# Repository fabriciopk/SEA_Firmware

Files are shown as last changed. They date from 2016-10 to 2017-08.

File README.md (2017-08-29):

# SEA_Firmware
Firmware for series elastic actuator, this board contains a stm32f103 microcontroller

#Installation(Upload using arduino IDE)

- Download arduino [IDE](https://www.arduino.cc/en/Main/Software)
- Download zip file containing the STM32 files from [here](https://github.com/fabriciopk/Arduino_STM32/archive/master.zip)
- Unzip in arduino hardware folder (arduino-1.6.xx/hardware/) and rename to Arduino_STM32
- Run the arduino IDE, and on the Tools menu, select the Boards manager (Tools > Boards > Boards Manager), and install the Arduino Zero(Arduino SAMD boards 32 bits cortex M3) from the list of available boards. You must do this step, it installs the arm-none-eabi-g++ toolchain!
- Copy AS5048A and DynamixelProtocol from [lib](https://github.com/fabriciopk/SEA_Firmware/tree/master/lib) folder to (arduino-1.6.xx/libraries/)
- Change the line #define BOARD_HAVE_SERIALUSB 0 in the file arduino-1.6.xx/hardware/STM32F1/cores/maple/boards.h 

#Setup Arduino IDE and board upload pins
- Board:STM32F103C Generic
- Variant:STM32F103C8
- Upload method: Stlink
- Open [src/src.ino](https://github.com/fabriciopk/SEA_Firmware/blob/master/src/src.ino)
- Pins for SWD(stlink v.2) setup:

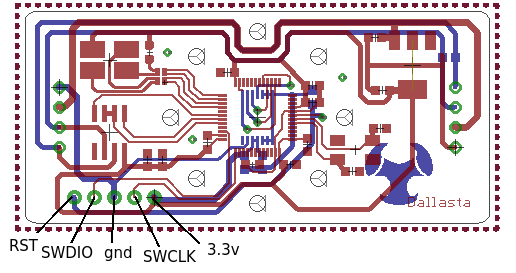
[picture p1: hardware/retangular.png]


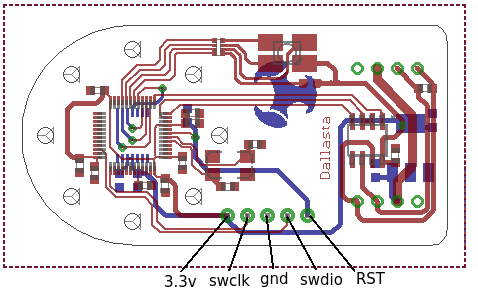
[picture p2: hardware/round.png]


NOTE: top-side of board.
#Board settings
```c++
#define SEA_ID 105 //define the board id in rs485 network
#define INVERTED
...
#define SEA_RECT //Type of the board, coment if is the rounded board
...
```
#Testing(linux)

Plug usb2Dinamyxel, power on the board.
```bash
cd test_board
make
./dynamixel_test ID_board
```

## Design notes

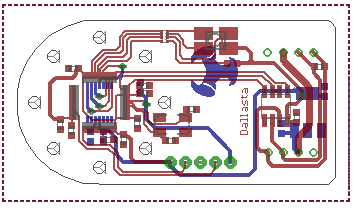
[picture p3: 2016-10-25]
hardware/eagle_files/OUT/sad.png

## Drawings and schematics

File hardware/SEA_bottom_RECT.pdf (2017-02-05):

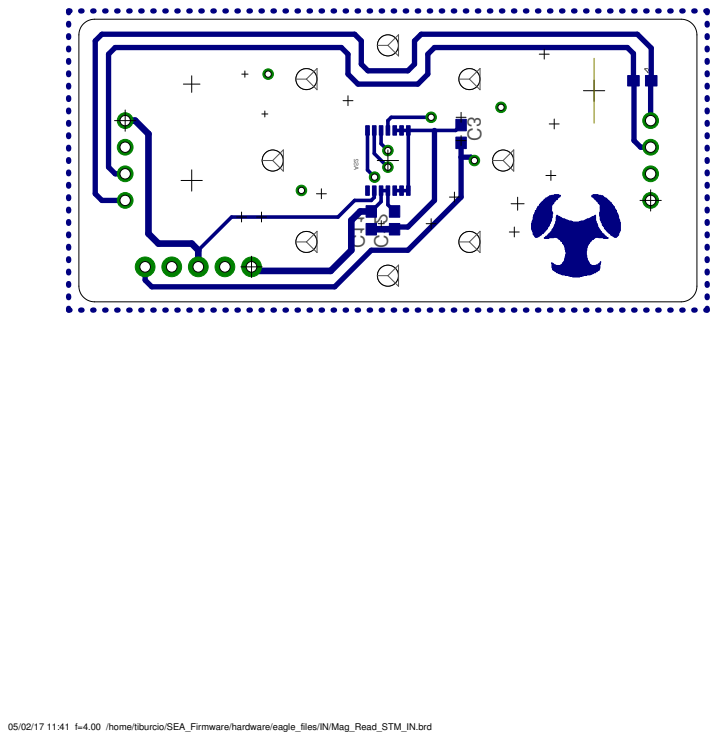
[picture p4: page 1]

05/02/17 11:41 f=4.00 /home/tiburcio/SEA_Firmware/hardware/eagle_files/IN/Mag_Read_STM_IN.brd

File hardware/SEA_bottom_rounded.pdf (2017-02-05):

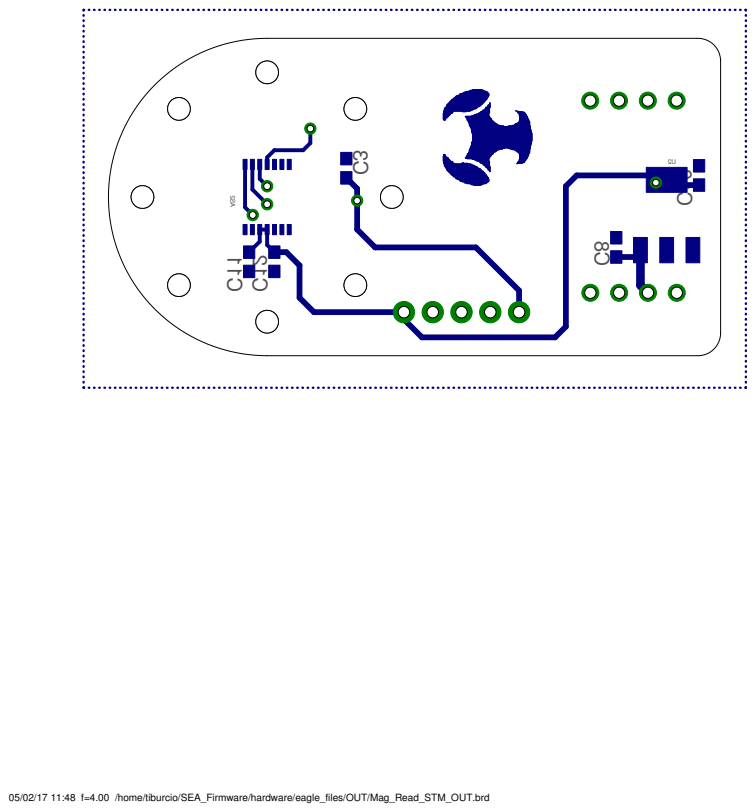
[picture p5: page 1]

05/02/17 11:48 f=4.00 /home/tiburcio/SEA_Firmware/hardware/eagle_files/OUT/Mag_Read_STM_OUT.brd

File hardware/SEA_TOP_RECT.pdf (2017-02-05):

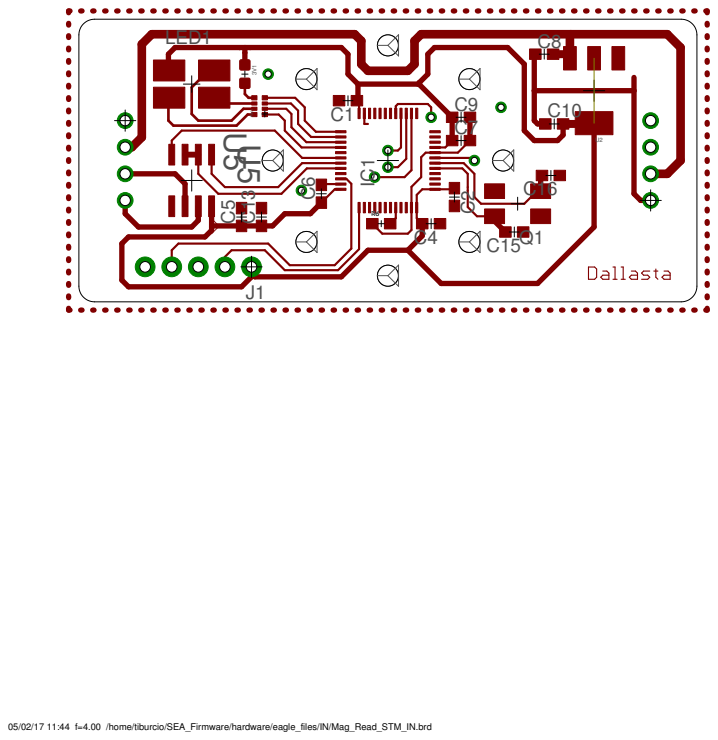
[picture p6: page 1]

05/02/17 11:44 f=4.00 /home/tiburcio/SEA_Firmware/hardware/eagle_files/IN/Mag_Read_STM_IN.brd

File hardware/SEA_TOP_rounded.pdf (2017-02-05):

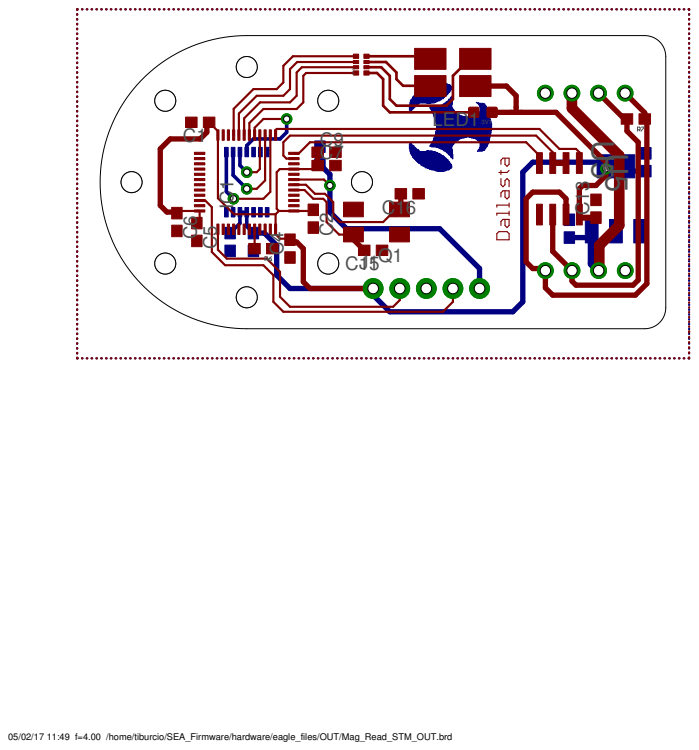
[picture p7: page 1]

05/02/17 11:49 f=4.00 /home/tiburcio/SEA_Firmware/hardware/eagle_files/OUT/Mag_Read_STM_OUT.brd

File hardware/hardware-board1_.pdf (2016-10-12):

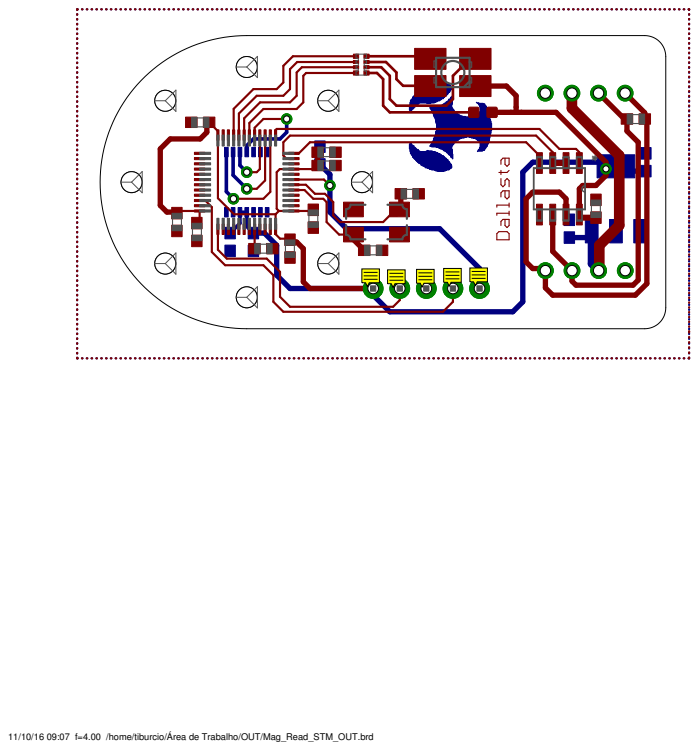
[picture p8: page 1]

11/10/16 09:07 f=4.00 /home/tiburcio/Área de Trabalho/OUT/Mag_Read_STM_OUT.brd

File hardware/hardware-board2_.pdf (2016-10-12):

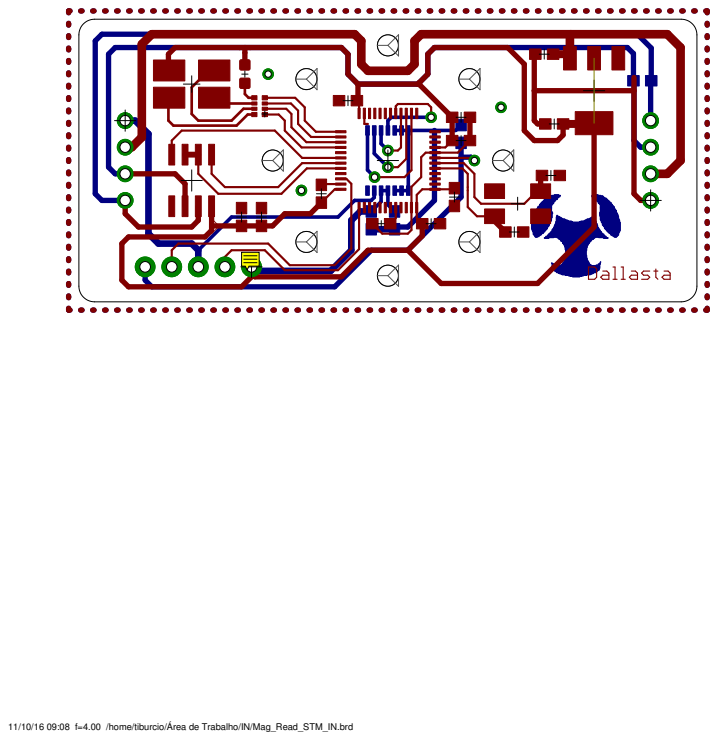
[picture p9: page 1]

11/10/16 09:08 f=4.00 /home/tiburcio/Área de Trabalho/IN/Mag_Read_STM_IN.brd

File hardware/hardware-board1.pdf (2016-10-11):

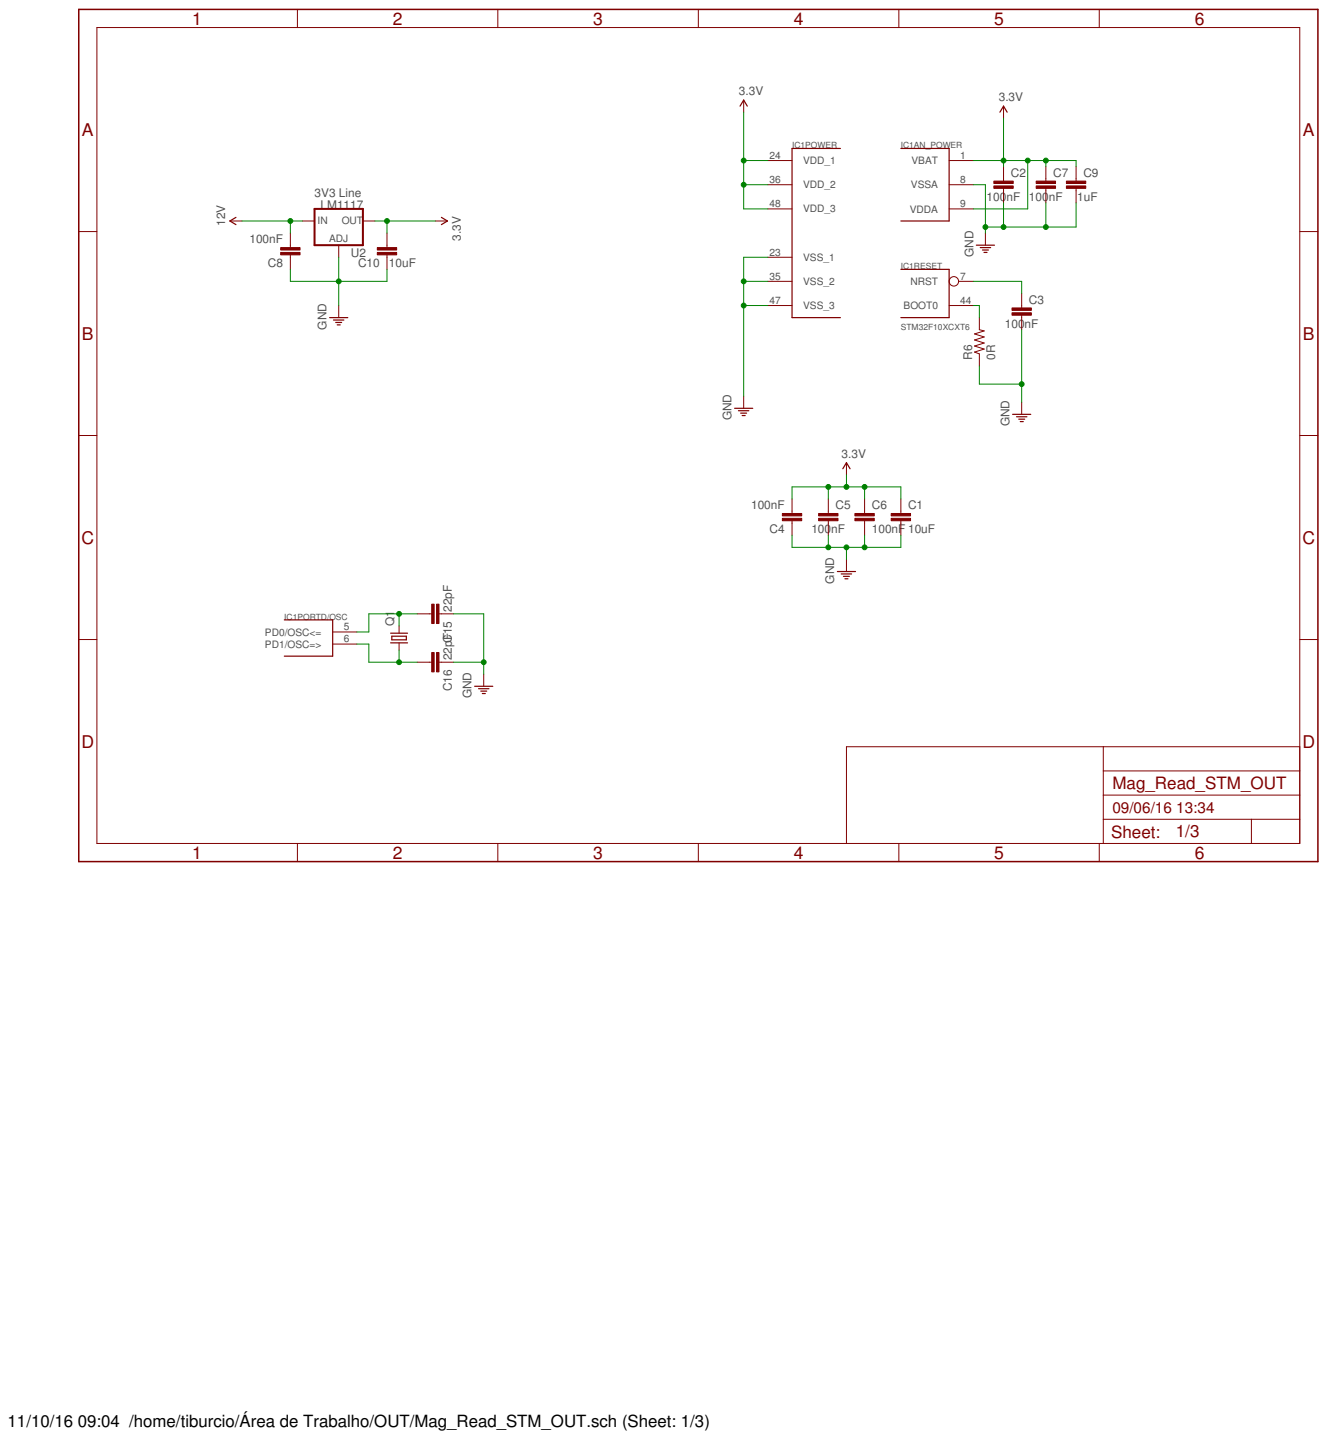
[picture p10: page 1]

11/10/16 09:04 /home/tiburcio/Área de Trabalho/OUT/Mag_Read_STM_OUT.sch (Sheet: 1/3)

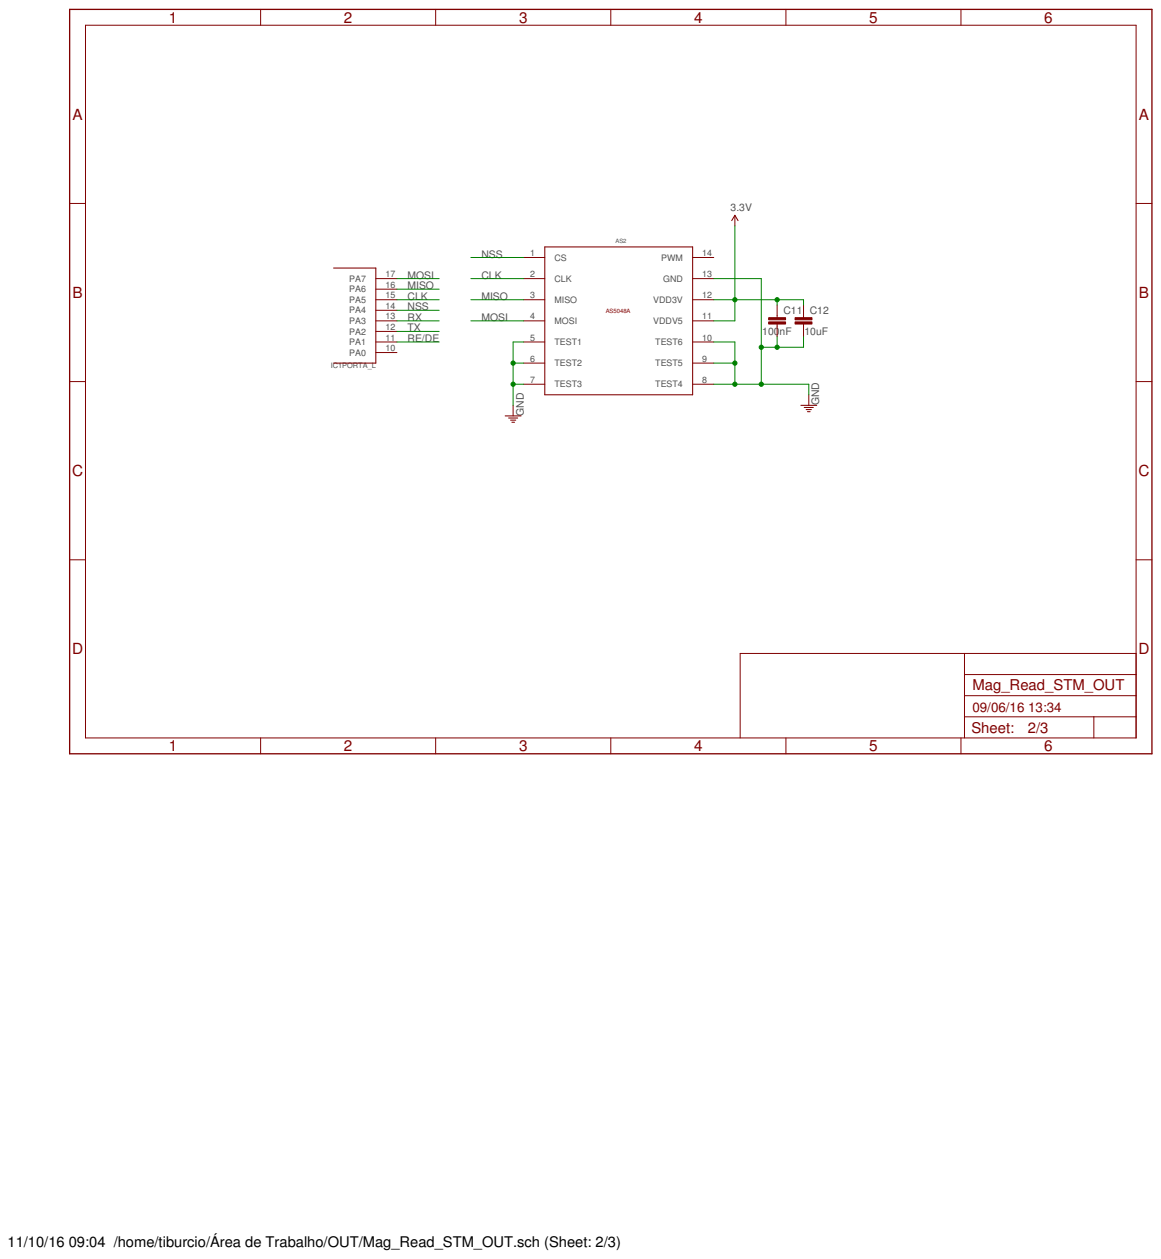
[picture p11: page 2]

11/10/16 09:04 /home/tiburcio/Área de Trabalho/OUT/Mag_Read_STM_OUT.sch (Sheet: 2/3)

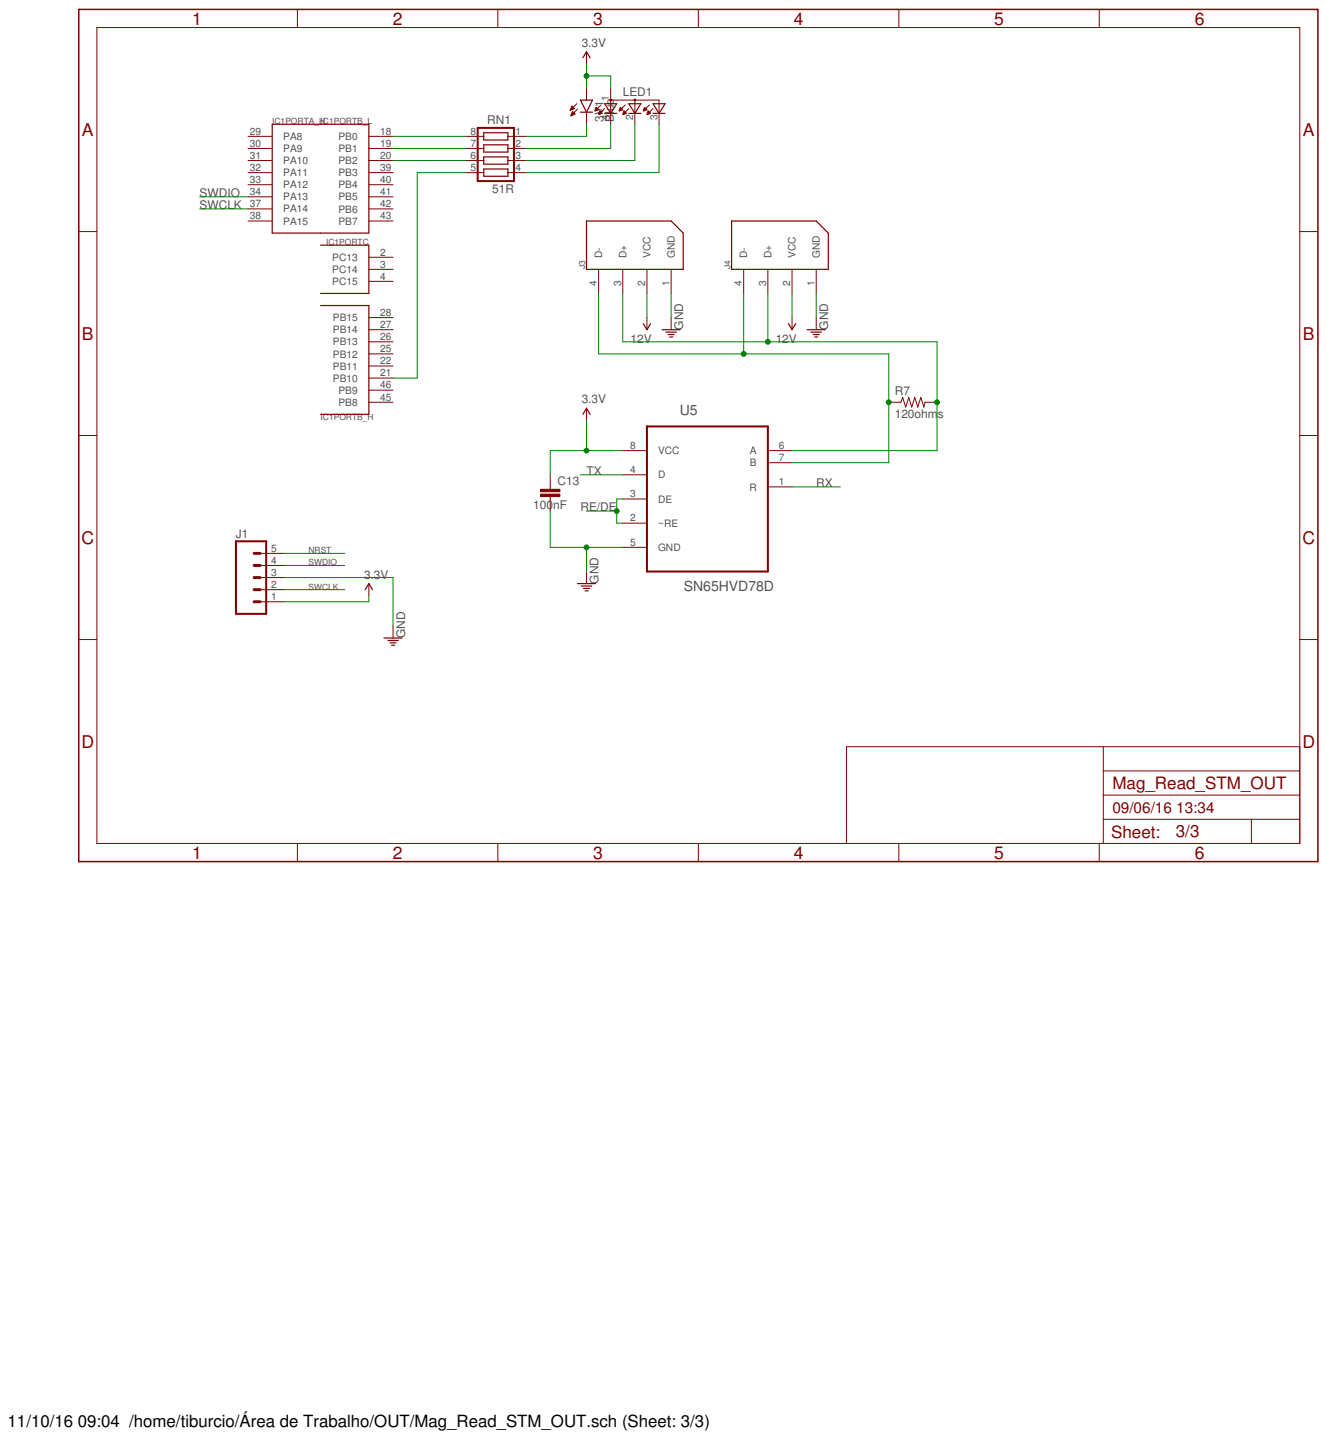
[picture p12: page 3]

19 PB2 7 | 2
20 PB3 6 | 3
39 PB4 5 | 4

11/10/16 09:04 /home/tiburcio/Área de Trabalho/OUT/Mag_Read_STM_OUT.sch (Sheet: 3/3)

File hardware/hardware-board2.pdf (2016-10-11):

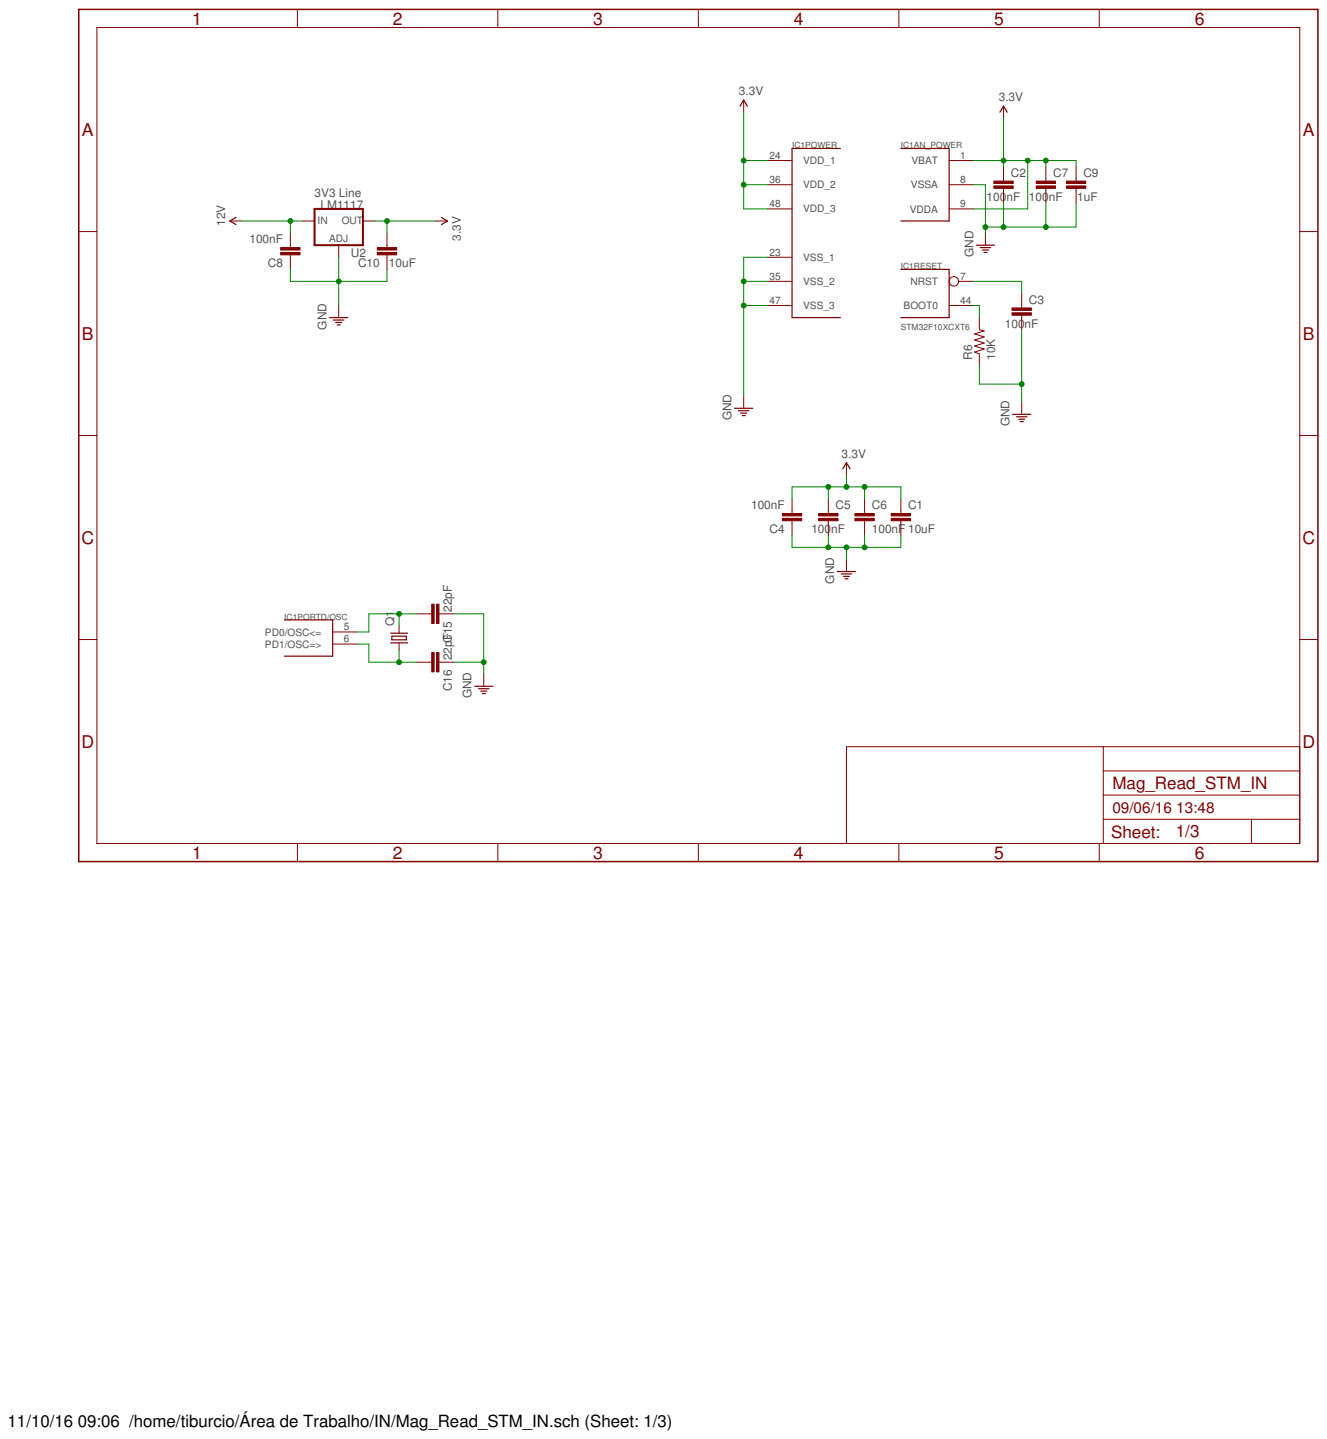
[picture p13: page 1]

11/10/16 09:06 /home/tiburcio/Área de Trabalho/IN/Mag_Read_STM_IN.sch (Sheet: 1/3)

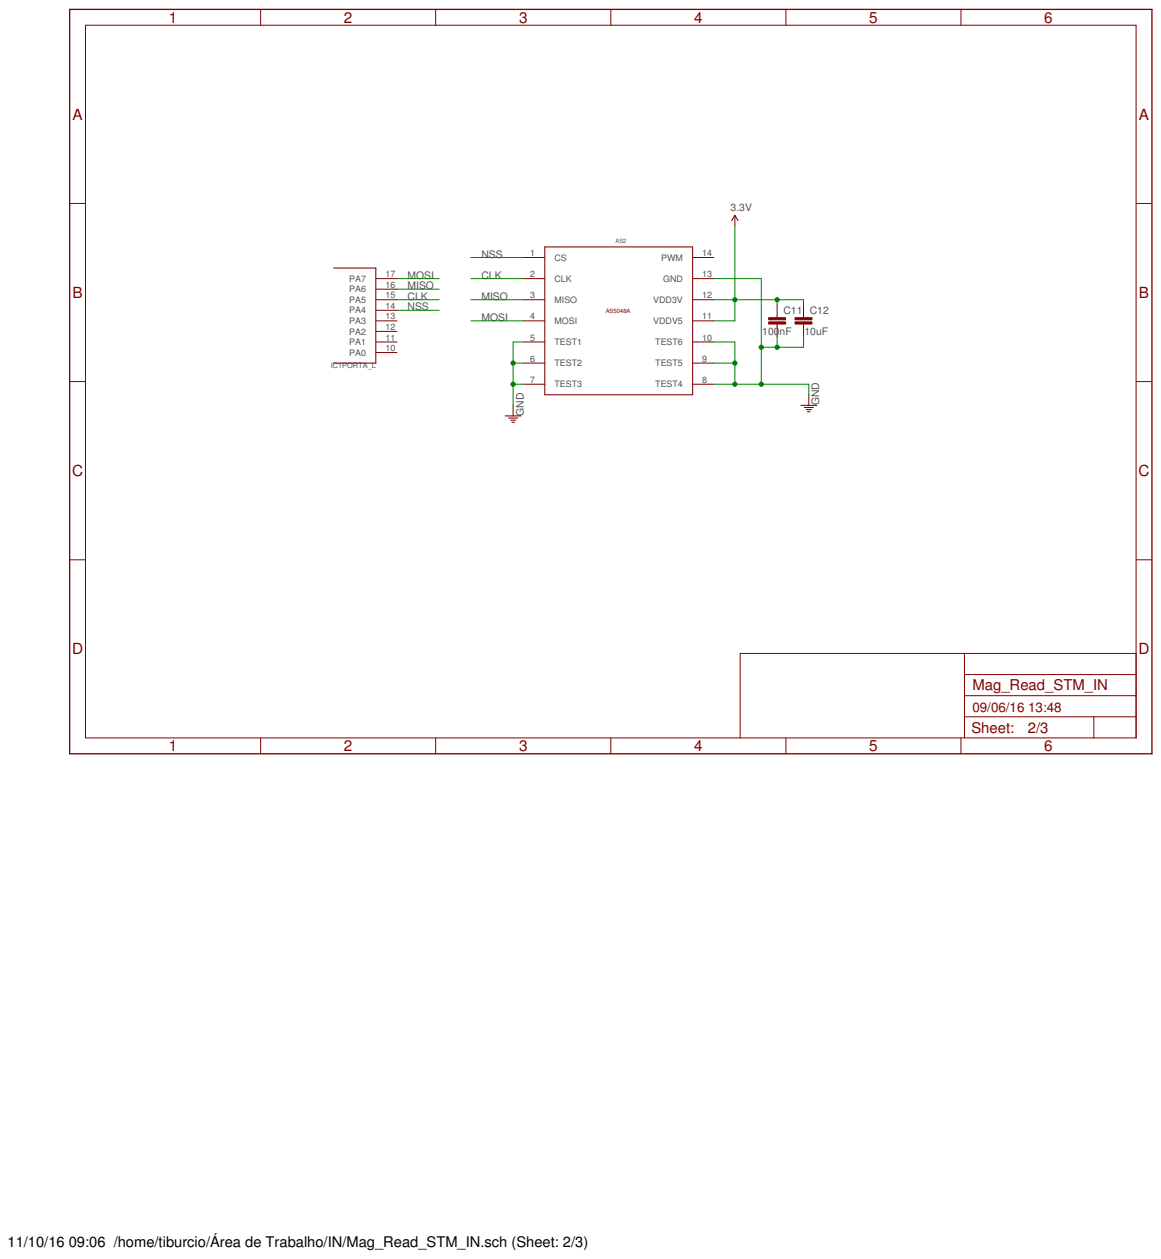
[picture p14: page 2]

11/10/16 09:06 /home/tiburcio/Área de Trabalho/IN/Mag_Read_STM_IN.sch (Sheet: 2/3)

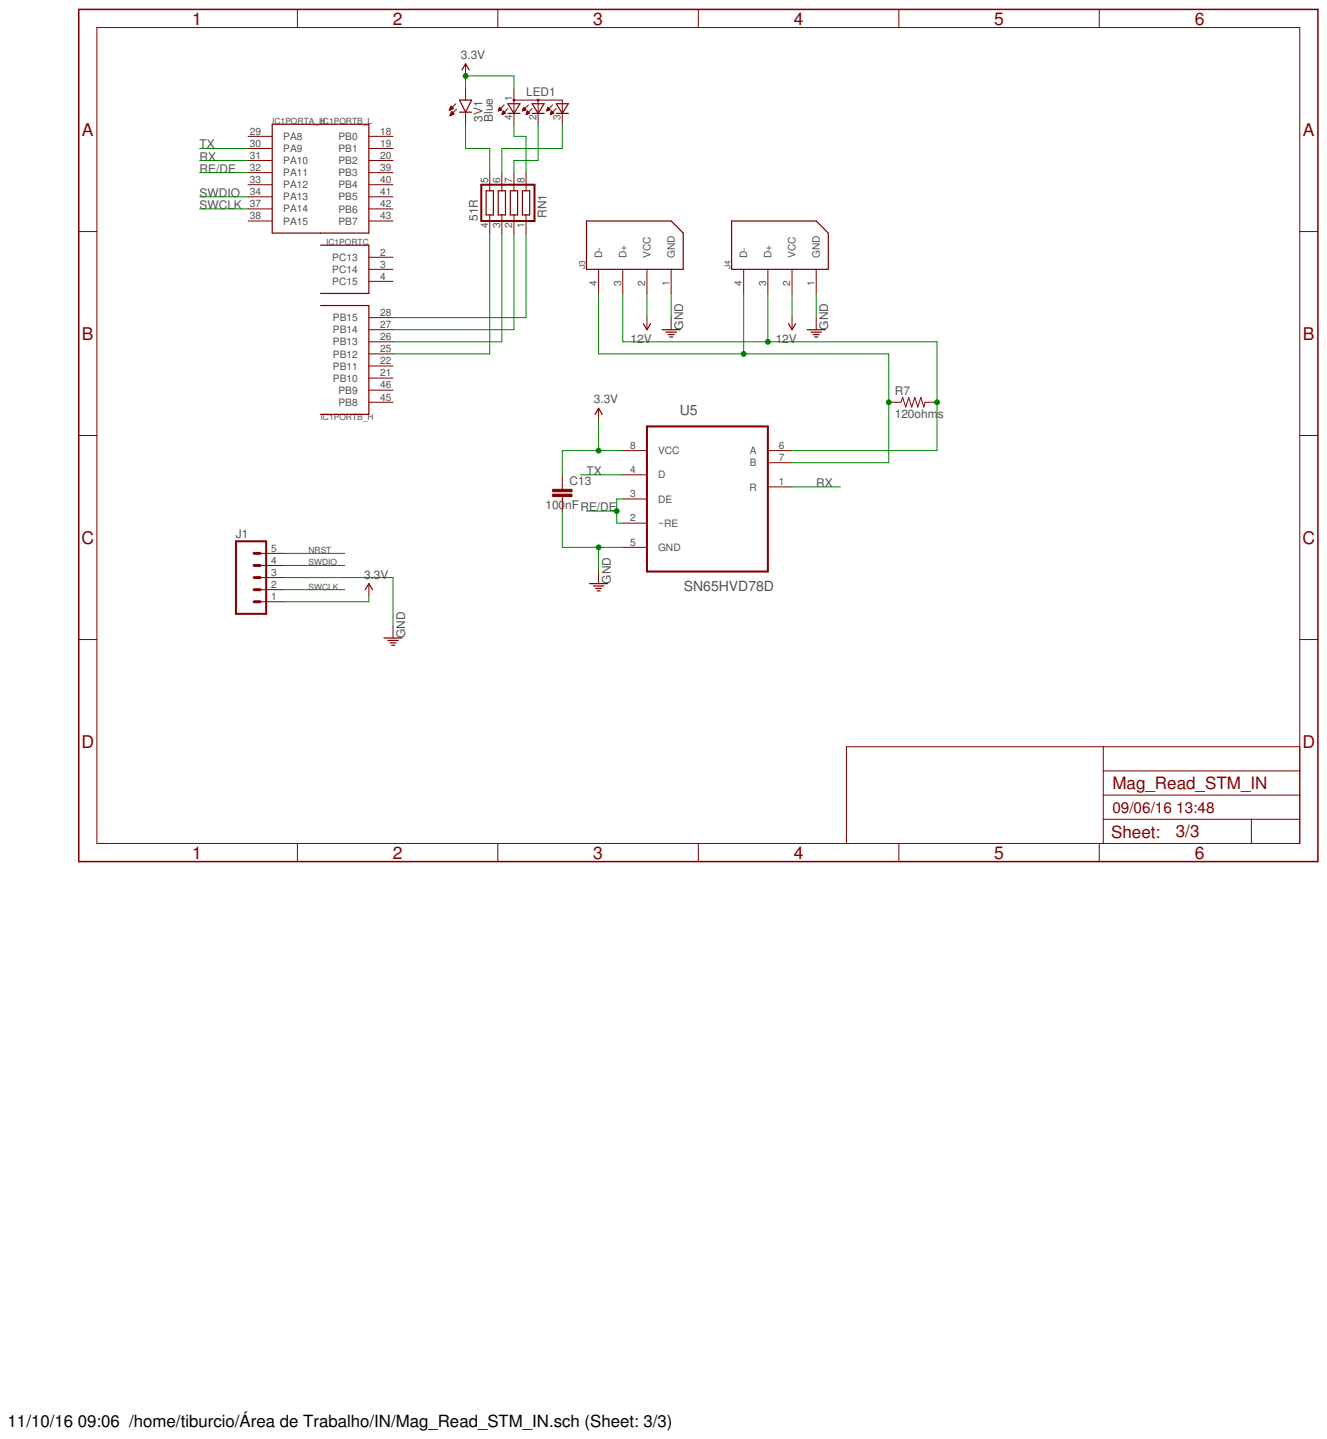
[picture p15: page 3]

27 PB15
26 PB14

11/10/16 09:06 /home/tiburcio/Área de Trabalho/IN/Mag_Read_STM_IN.sch (Sheet: 3/3)

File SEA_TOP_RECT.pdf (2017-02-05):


05/02/17 11:43 f=4.00 /home/tiburcio/SEA_Firmware/hardware/eagle_files/IN/Mag_Read_STM_IN.brd

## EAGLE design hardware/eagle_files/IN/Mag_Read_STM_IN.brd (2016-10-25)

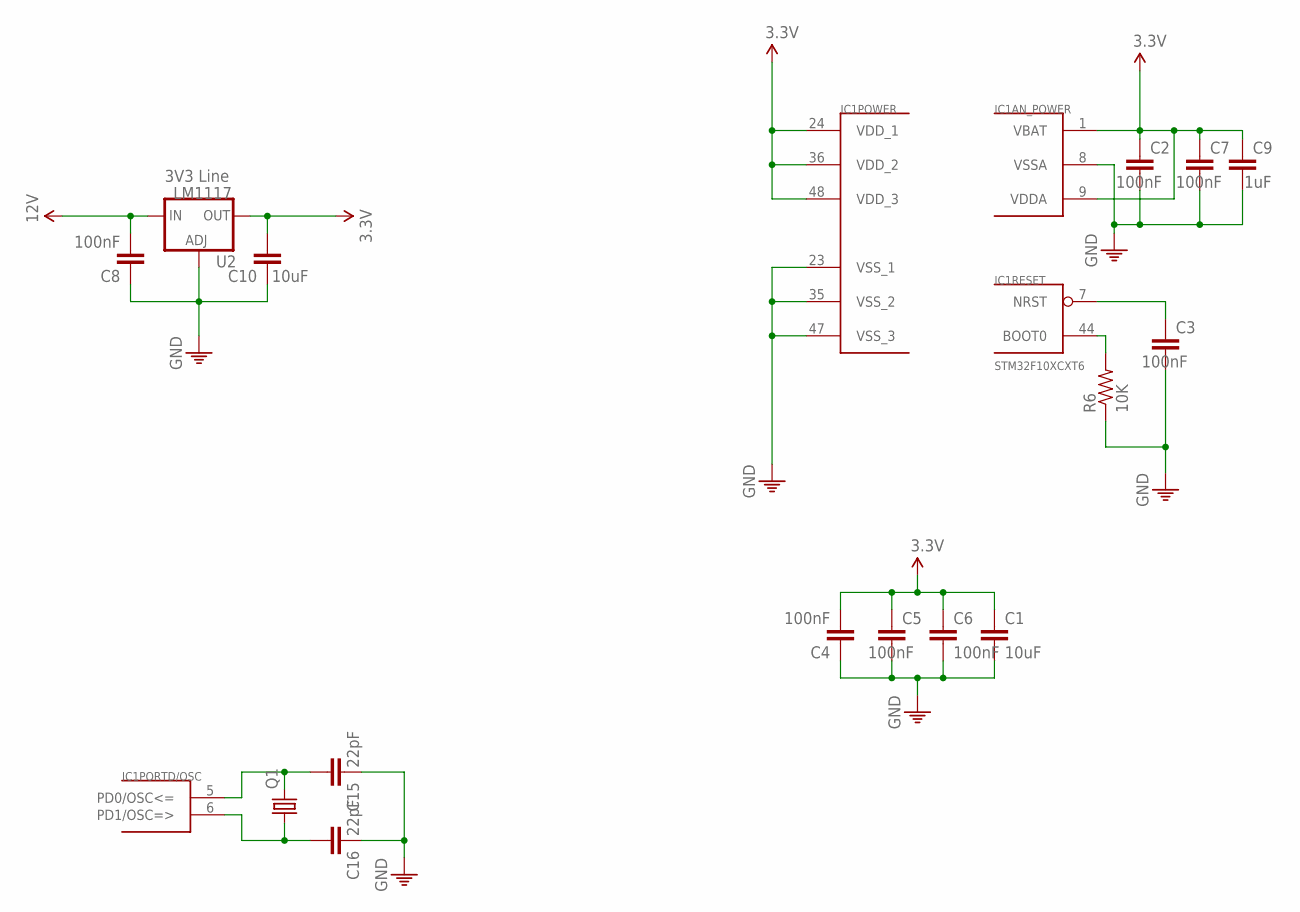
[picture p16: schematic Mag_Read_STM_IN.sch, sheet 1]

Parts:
C1, C10: 10uF; C0603
C2, C3, C4, C5, C6, C7, C8: 100nF; C0603
C9: 1uF; C0603
C15, C16: 22pF; C0603
IC1: STM32F10XCXT6; TQFP48
Q1: CRYSTALCTS406; CTS406
R6: 10K; 0603-RES
U2: LM1117; SOT223

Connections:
3.3V: C1.1, C2.1, C4.2, C5.1, C6.1, C7.1, C9.1, C10.2, IC1.1 (VBAT), IC1.9 (VDDA), IC1.24 (VDD_1), IC1.36 (VDD_2), IC1.48 (VDD_3), U2.2 (OUT), U2.4 (OUT); also elsewhere on the board
12V: C8.2, U2.3 (IN); also elsewhere on the board
GND: C1.2, C2.2, C3.2, C4.1, C5.2, C6.2, C7.2, C8.1, C9.2, C10.1, C15.1, C16.1, IC1.8 (VSSA), IC1.23 (VSS_1), IC1.35 (VSS_2), IC1.47 (VSS_3), R6.1, U2.1 (ADJ); also elsewhere on the board
unnamed: C15.2, IC1.5 (PD0/OSC<=), Q1.3 (2)
unnamed: C16.2, IC1.6 (PD1/OSC=>), Q1.1
unnamed: IC1.44 (BOOT0), R6.2
NRST: C3.1, IC1.7 (NRST); also elsewhere on the board

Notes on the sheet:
3V3 Line

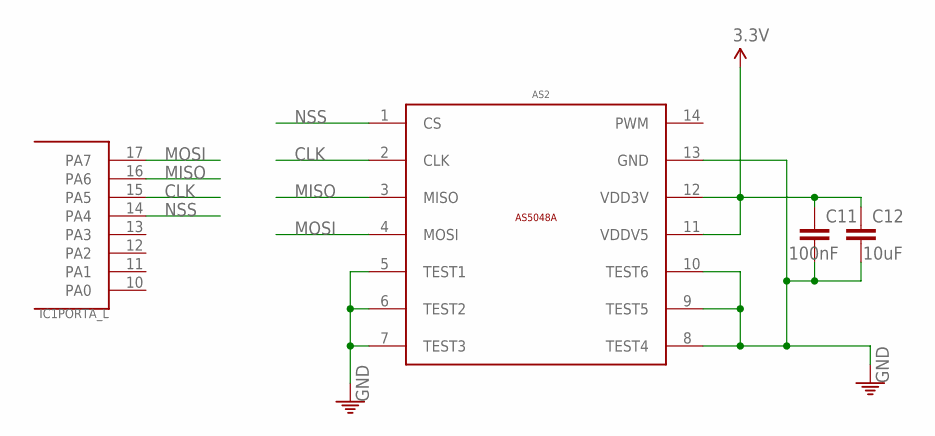
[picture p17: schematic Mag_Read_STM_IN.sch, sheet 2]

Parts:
AS2: AS5048A_MAGNETIC_ROTARY_ENCODERTSSOP14; AS5048A_14-TSSOP
C11: 100nF; C0603
C12: 10uF; C0603
IC1: STM32F10XCXT6; TQFP48

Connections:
3.3V: AS2.11 (VDDV5), AS2.12 (VDD3V), C11.1, C12.1; also elsewhere on the board
CLK: AS2.2 (CLK), IC1.15 (PA5)
GND: AS2.5 (TEST1), AS2.6 (TEST2), AS2.7 (TEST3), AS2.8 (TEST4), AS2.9 (TEST5), AS2.10 (TEST6), AS2.13 (GND), C11.2, C12.2; also elsewhere on the board
MISO: AS2.3 (MISO), IC1.16 (PA6)
MOSI: AS2.4 (MOSI), IC1.17 (PA7)
NSS: AS2.1 (CS), IC1.14 (PA4)

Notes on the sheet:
MISO
MOSI
NSS
CLK

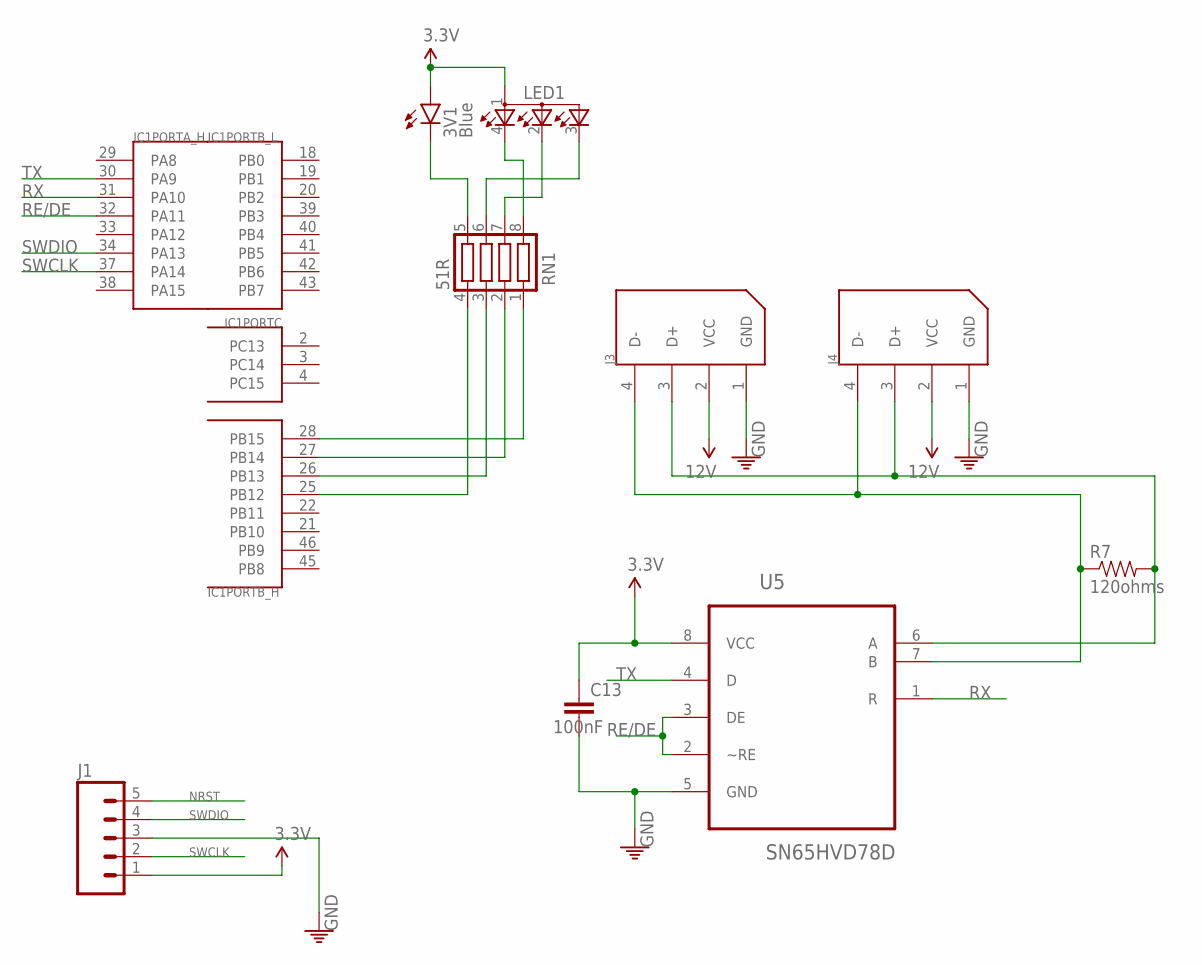
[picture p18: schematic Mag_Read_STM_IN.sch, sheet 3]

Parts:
3V1: Blue; LED-0603
C13: 100nF; C0603
IC1: STM32F10XCXT6; TQFP48
J1: M05PTH; 1X05
J3, J4: 22-03-5045; 5267-4
LED1: TOPLED-3; P-LCC-4-3
R7: 120ohms; 0603-RES
RN1: 51R; CAY10-XXXJ4
U5: SN65HVD78D; SOIC127P600X175-8N

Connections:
3.3V: 3V1.A, C13.1, J1.1, LED1.1 (A2), U5.8 (VCC); also elsewhere on the board
12V: J3.2 (VCC), J4.2 (VCC); also elsewhere on the board
D+: J3.3 (D+), J4.3 (D+), R7.2, U5.6 (A)
D-: J3.4 (D-), J4.4 (D-), R7.1, U5.7 (B)
GND: C13.2, J1.3, J3.1 (GND), J4.1 (GND), U5.5 (GND); also elsewhere on the board
unnamed: 3V1.C, RN1.5
unnamed: IC1.28 (PB15), RN1.1
unnamed: IC1.27 (PB14), RN1.2
unnamed: IC1.26 (PB13), RN1.3
unnamed: LED1.3 (CGREEN), RN1.6
unnamed: LED1.2 (CBLUE), RN1.7
unnamed: LED1.4 (CRED), RN1.8
unnamed: IC1.25 (PB12), RN1.4
NRST: J1.5; also elsewhere on the board
RE/DE: IC1.32 (PA11), U5.2 (~RE), U5.3 (DE)
RX: IC1.31 (PA10), U5.1 (R)
SWCLK: IC1.37 (PA14), J1.2
SWDIO: IC1.34 (PA13), J1.4
TX: IC1.30 (PA9), U5.4 (D)

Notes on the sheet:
RE/DE
SWCLK
SWDIO
NRST

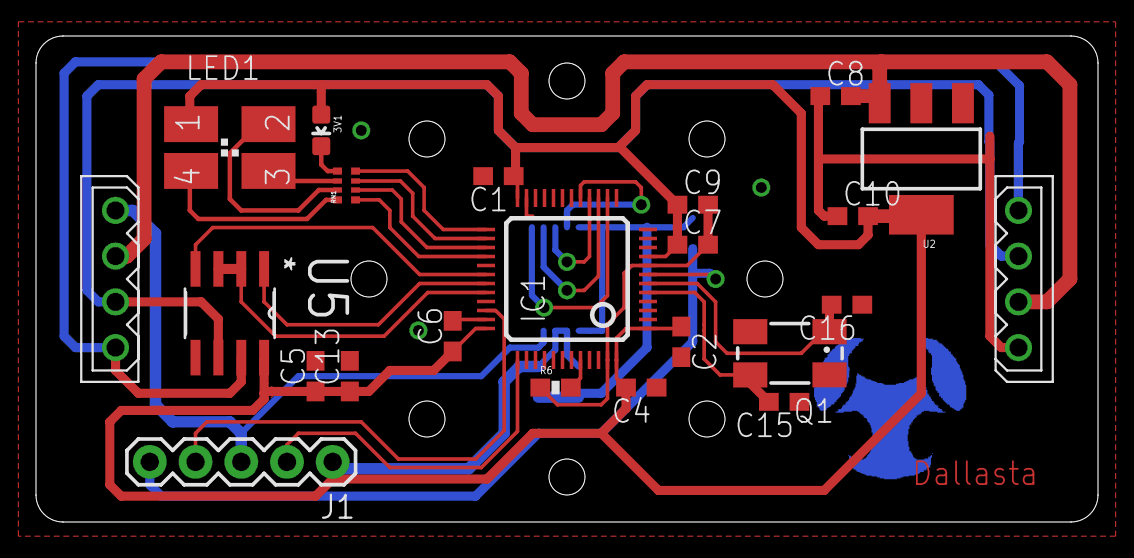
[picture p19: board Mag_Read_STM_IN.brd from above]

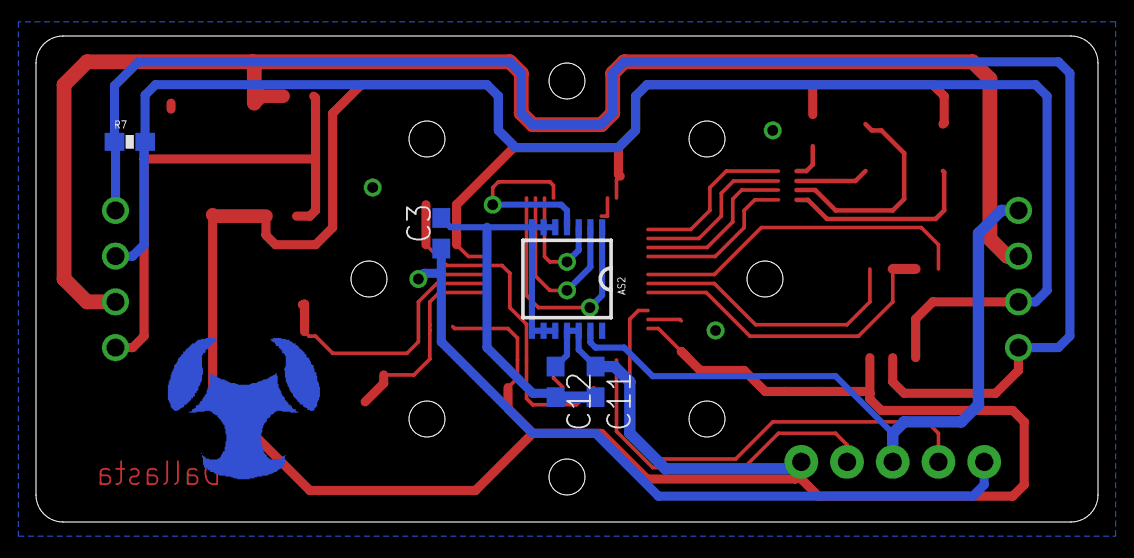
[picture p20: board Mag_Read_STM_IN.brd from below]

Board: 2 copper layers, 59.0 x 27.0 mm, 28 parts (5 on the bottom side), 26 nets.

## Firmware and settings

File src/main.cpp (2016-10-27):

#include <DynamixelProtocol.h>
#include <AS5048A.h>

//TODO check if serial of maple core is in the correct pins
//HardwareSerial Serial1(&rx_buffer1, &UBRR1H, &UBRR1L, &UCSR1A, &UCSR1B, &UDR1, RXEN1, TXEN1, RXCIE1, UDRE1, U2X1);

#define SEA_ID 105
#define INVERTED
#define SEA_INSTRUCTION 0x24

#define SEA_RECT

#ifdef SEA_RECT

#define LED PB12
#define LED_RED PB14
#define LED_BLUE PB15
#define LED_GREEN PB13
#define SERIAL Serial1 //Tem que mudar dentro da biblioteca do dynamixel tambem (Serial)
#define EN PA11

#else

#define LED PB0
#define LED_RED PB2
#define LED_BLUE PB1
#define LED_GREEN PB10
#define SERIAL Serial2 //Tem que mudar dentro da biblioteca do dynamixel tambem (Serial)
#define EN PA1

#endif

#define SPI_NSS PA4
#define BAUDRATE_DX 1000000

int RGB[3] = {LED_RED, LED_GREEN, LED_BLUE};
int color = 0;

AS5048A mag(SPI_NSS);
DynamixelProtocol dxl(BAUDRATE_DX, SEA_ID, SERIAL);

void blink(int times)
{
  for (int i = 0 ; i < times ; i++)
  {
    digitalWrite(LED, LOW);
    delay(125);
    digitalWrite(LED, HIGH);
    delay(125);
  }
  delay(500);
}

void setup()
{
  delay(1000);
  pinMode(LED, OUTPUT);
  pinMode(LED_RED, OUTPUT);
  pinMode(LED_GREEN, OUTPUT);
  pinMode(LED_BLUE, OUTPUT);
  //Enable rs485
  pinMode(EN, OUTPUT);
  digitalWrite(EN, LOW);

  mag.init();
  dxl.init();
  blink(SEA_ID - 100);
  digitalWrite(LED_RED, HIGH);
  digitalWrite(LED_GREEN, HIGH);
  digitalWrite(LED_BLUE, HIGH);
}

void loop() {
#ifndef INVERTED
  word val = mag.getRawRotation();
#else
  word val = 8192 - mag.getRawRotation();
#endif
  dxl.checkMessages();
  if (dxl.instruction != DXL_NO_DATA)
  {

    switch (dxl.instruction)
    {
      case DXL_PING:
        digitalWrite(EN, HIGH);
        dxl.sendStatusPacket(0x00, NULL, 0);
        SERIAL.waitDataToBeSent();
        digitalWrite(EN, LOW);
        break;
      case DXL_READ_DATA:
        if (dxl.total_parameters == 2 && dxl.parameters[1] == 2)
        {
          unsigned char values[2];
          switch (dxl.parameters[0])
          {
            case SEA_INSTRUCTION:
              values[0] = (unsigned char)val;
              values[1] = (unsigned char)(val >> 8);
              digitalWrite(LED, HIGH);
              break;
            case 0x00:
              values[0] = 54;
              values[1] = 1;
              break;
            case 0x01:
              values[0] = 0;
              values[1] = 1;
              break;
            default:
              values[0] = 0;
              values[1] = 0;
              break;
          }
          digitalWrite(EN, HIGH);
          dxl.sendStatusPacket(0x00, values, 2);
          SERIAL.waitDataToBeSent();
          digitalWrite(EN, LOW);
          digitalWrite(RGB[color], LOW);
          color = (color + 1) % 3;
          digitalWrite(RGB[color], HIGH);
        }
        break;
      case DXL_WRITE_DATA:
        break;
      case DXL_REG_WRITE:
        break;
      case DXL_ACTION:
        break;
      case DXL_RESET:
        break;
      case DXL_SYNC_WRITE:
        break;
      default:
        break;
    }
  } else {
    digitalWrite(LED_RED, HIGH);
    digitalWrite(LED_GREEN, HIGH);
    digitalWrite(LED_BLUE, HIGH);
    digitalWrite(LED, HIGH);
  }
  digitalWrite(LED, HIGH);
}

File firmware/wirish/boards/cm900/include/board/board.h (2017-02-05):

/******************************************************************************
 * The MIT License
 *
 * Copyright (c) 2011 LeafLabs, LLC.
 *
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
 * THE SOFTWARE IS PROVIDED "AS IS", WITHOUT WARRANTY OF ANY KIND,
 * EXPRESS OR IMPLIED, INCLUDING BUT NOT LIMITED TO THE WARRANTIES OF
 * MERCHANTABILITY, FITNESS FOR A PARTICULAR PURPOSE AND
 * NONINFRINGEMENT. IN NO EVENT SHALL THE AUTHORS OR COPYRIGHT HOLDERS
 * BE LIABLE FOR ANY CLAIM, DAMAGES OR OTHER LIABILITY, WHETHER IN AN
 * ACTION OF CONTRACT, TORT OR OTHERWISE, ARISING FROM, OUT OF OR IN
 * CONNECTION WITH THE SOFTWARE OR THE USE OR OTHER DEALINGS IN THE
 * SOFTWARE.
 *****************************************************************************/


/*
 * CM900.h
 *
 *  Created on: 2012. 10. 14.
 *      Author: ROBOTIS[sm6787@robotis.com]
 *      ported from maple.h(leaflabs.com)
 *      @brief  Private include file for cm-900 in boards.h
 */

#ifndef CM_900_H_
#define CM_900_H_

//#include "gpio.h"


#define CYCLES_PER_MICROSECOND  72
#define SYSTICK_RELOAD_VAL      71999 /* takes a cycle to reload */
/*
 * [ROBOTIS][CHANGE] CM-900 Do not have built-in button.
 * 2013-04-22
 * */
#define BOARD_BUTTON_PIN        23//38
#define BOARD_LED_PIN           16

/* Number of USARTs/UARTs whose pins are broken out to headers */
//#define BOARD_NR_USARTS         3

/* Default USART pin numbers (not considering AFIO remap) */
#define BOARD_USART1_TX_PIN     9   //D9(PA9)
#define BOARD_USART1_RX_PIN     10	//D10(PA10)
#define BOARD_USART2_TX_PIN     2	//D2 (PA2)
#define BOARD_USART2_RX_PIN     3	//D3 (PA3)
#define BOARD_USART3_TX_PIN     24	//D24 (PB10)
#define BOARD_USART3_RX_PIN     25	//D25 (PB11)

/* Number of SPI ports */
//#define BOARD_NR_SPI            2

/* Default SPI pin numbers (not considering AFIO remap) */
#define BOARD_SPI1_NSS_PIN      10 //D10 (PA4)
#define BOARD_SPI1_MOSI_PIN     11 //D11 PA7
#define BOARD_SPI1_MISO_PIN     12 //D12 PA6
#define BOARD_SPI1_SCK_PIN      13 //D13 PA5
#define BOARD_SPI2_NSS_PIN      26 //D26 PB12
#define BOARD_SPI2_MOSI_PIN     29 //D29 PB15
#define BOARD_SPI2_MISO_PIN     28 //D28 PB14
#define BOARD_SPI2_SCK_PIN      27 //D27 PB13

/* Total number of GPIO pins that are broken out to headers and
 * intended for general use. */
#define BOARD_NR_GPIO_PINS      32//44

/* Number of pins capable of PWM output */
#define BOARD_NR_PWM_PINS       15

/* Number of pins capable of ADC conversion */
#define BOARD_NR_ADC_PINS       10

/* Number of pins already connected to external hardware.  For Maple,
 * these are just BOARD_LED_PIN and BOARD_BUTTON_PIN. */
#define BOARD_NR_USED_PINS       1

/* Debug port pins */
#define BOARD_JTMS_SWDIO_PIN    11
#define BOARD_JTCK_SWCLK_PIN    12
#define BOARD_JTDI_PIN          13
#define BOARD_JTDO_PIN          17
#define BOARD_NJTRST_PIN        18

#define BOARD_USB_DISC_DEV      GPIOC
#define BOARD_USB_DISC_BIT      13

void boardInit(void);

#define BOARD_DYNAMIXEL_DIR     19
#define BOARD_DYNAMIXEL_TX      20
#define BOARD_DYNAMIXEL_RX      21

#endif /* CM_900_H_ */

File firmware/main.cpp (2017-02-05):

#include <wirish/wirish.h>
#include <libmaple/adc.h>
#include <libmaple/timer.h>

#define LED PB1

void setup() {}
void loop() {
  digitalWrite(LED, LOW);
  delay(125);
  digitalWrite(LED, HIGH);
  delay(125);
}


int main(void) {
    setup();

    while (true) {
        loop();
    }

    return 0;
}

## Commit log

2016-10-10 Added dynamixel and magnetometer libraries
2016-10-10 New firmware for stm32f103c8
2016-10-11 Added new makefile for flash the device
2016-10-25 Added new functions
    [Mag_Read_STM_IN.brd, Mag_Read_STM_IN.sch, Mag_Read_STM_OUT.brd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]
2017-02-05 src change
    [flash_0.3.cfg, flash_0.4.cfg]

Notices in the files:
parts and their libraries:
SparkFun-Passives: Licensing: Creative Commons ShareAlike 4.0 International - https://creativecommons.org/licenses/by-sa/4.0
